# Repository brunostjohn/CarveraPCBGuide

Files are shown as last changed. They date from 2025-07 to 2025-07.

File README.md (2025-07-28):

# How to make double-sided PCBs at home with a Carvera (Air)

This is a super in-progress guide for doing this. There's probably many better ways to do this, this is just what's worked for me.

## Table of Contents

- [How to make double-sided PCBs at home with a Carvera (Air)](#how-to-make-double-sided-pcbs-at-home-with-a-carvera-air)
  - [Table of Contents](#table-of-contents)
- [Materials, Tools, and Software](#materials-tools-and-software)
  - [Software](#software)
  - [Materials](#materials)
  - [Tools](#tools)
- [Preparation](#preparation)
  - [Making a PCB-friendly wasteboard.](#making-a-pcb-friendly-wasteboard)
  - [Making sure copper chips aren't fucking with our mill quality.](#making-sure-copper-chips-arent-fucking-with-our-mill-quality)
- [Going from PCB to Gcode.](#going-from-pcb-to-gcode)
  - [Creating your PCB in KiCAD](#creating-your-pcb-in-kicad)
    - [Quick note about text](#quick-note-about-text)
    - [Board setup](#board-setup)
    - [Pre-export work](#pre-export-work)
    - [Actually exporting the damn thing.](#actually-exporting-the-damn-thing)
  - [Importing your PCB to FlatCAM.](#importing-your-pcb-to-flatcam)
    - [Aligning your sides](#aligning-your-sides)
  - [Adding alignment drills.](#adding-alignment-drills)
  - [Actually making gcode for the align drills.](#actually-making-gcode-for-the-align-drills)
    - [Generating g-code for the front side of the PCB.](#generating-g-code-for-the-front-side-of-the-pcb)
  - [Generating g-code for the back side of the PCB.](#generating-g-code-for-the-back-side-of-the-pcb)
  - [Generating gcode for removing the front solder mask.](#generating-gcode-for-removing-the-front-solder-mask)
  - [Generating the gcode for removing the back solder mask.](#generating-the-gcode-for-removing-the-back-solder-mask)
  - [Generating the gcode for lasering on the front silkscreen.](#generating-the-gcode-for-lasering-on-the-front-silkscreen)
  - [Generating the gcode for lasering on the back silkscreen.](#generating-the-gcode-for-lasering-on-the-back-silkscreen)
  - [Generating the gcode for drills and edge cuts.](#generating-the-gcode-for-drills-and-edge-cuts)
- [Milling the board, lasering the board, and other random side quests.](#milling-the-board-lasering-the-board-and-other-random-side-quests)
  - [Attaching the fixture \& adding the fan.](#attaching-the-fixture--adding-the-fan)
  - [Attaching the PCB.](#attaching-the-pcb)
  - [Finding the 0 point and setting up work coordinates.](#finding-the-0-point-and-setting-up-work-coordinates)
  - [Drilling alignment holes.](#drilling-alignment-holes)
  - [Front copper isolation.](#front-copper-isolation)
  - [Front non-copper clearing](#front-non-copper-clearing)
  - [Back copper isoltion \& NCC.](#back-copper-isoltion--ncc)
  - [Applying the back solder mask.](#applying-the-back-solder-mask)

# Materials, Tools, and Software

## Software

- KiCAD
- Makera's CAM
- Fusion 360
- FlatCAM

  This guide uses the 8.994 beta version of FlatCAM. There _will_ be differences between other versions, but the workflow should stay roughly the same.

## Materials

- Copper-clad FR4, duh.
- UV-curable solder mask (both in target solder mask colour and white, you'll see why).
- Some random ass wood for milling the PCB fixture. (should fit on the Carvera bed)
- TPU to make a spindle fan
- Double sided tape.
- An acetate sheet.

## Tools

- The Carvera Air.
- 3D printer (optional)
- A UV light.
- Shop vac (optional)
- The sanding block that came with the Carvera
- Carvera's Laser Module.
- A 0.2mm corn bit/endmill.
- A 2mm/4mm drill bit.
- Makera's solder mask removal bit.
- Corn bits in other various sizes.
- Drill bits also in other various sizes.
- Something to scrape the PCB off the fixture after the double sided tape. I'm using a 3D printer bed scraper.

# Preparation

## Making a PCB-friendly wasteboard.

The MDF wasteboard on the Carvera isn't super friendly to milling PCBs so we need to make our own thing to which we will attach PCBs. Fortunately enough, I've solved this problem already by making a Carvera friendly thing that can accomodate large-ish PCBs and screws into the bed. It isn't entirely my own creation, it's based on [this guide's](https://hackaday.io/project/202478/instructions) fixture created by [Vedran](https://hackaday.io/vedranMv). I only modified it to hold larger PCBs. You don't need to mill all the holes, it's really only the screwholes that matter. Here's a photo of mine.

Fixture

I made it out of some random wood my landlord had in her shed. Just make if flat enough and you'll be fine.

You can get the [Fusion project here](./projects_and_gcode/fusion/PCB%20fixture%20thing.f3d) or the [STEP file here](./projects_and_gcode/step/PCB%20fixture%20thing.step).

## Making sure copper chips aren't fucking with our mill quality.

When the bit you're using mills it's own chips (or in this case, dust), you get more burrs and more bullshit. To prevent this you can either use a vaccuum attached to your Carvera or a delightful fan.

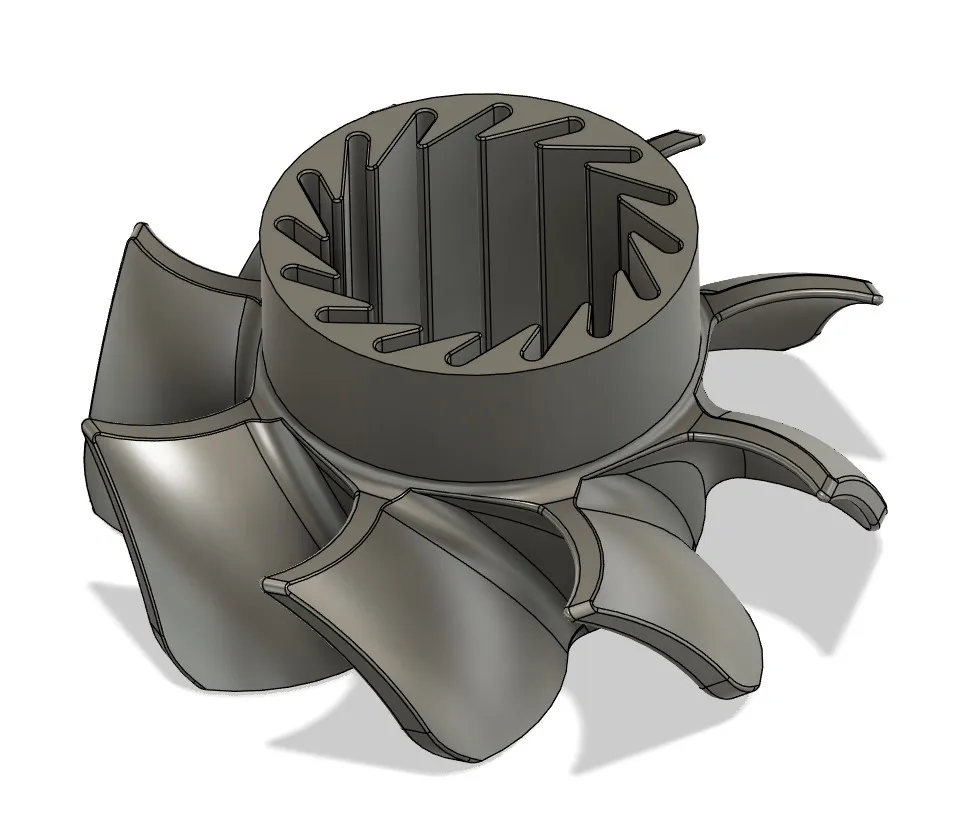
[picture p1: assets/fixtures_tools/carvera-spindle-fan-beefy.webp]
Spindle fan


[RedGT500](https://www.printables.com/@RedGT500_1977691) has already made a great fix to this. A 3D printable fan made out of TPU that's made to go on your spindle. You can even see mine in that photo of the fixture above. You can download it [here](https://www.printables.com/model/1332188-carvera-spindle-fan-beefy-version/files). I've also reuploaded it [here](./projects_and_gcode/step/Spindle%20Fan.step) to protect against link rot.

# Going from PCB to Gcode.

## Creating your PCB in KiCAD

Teaching you to actually make PCBs is outside the scope of this guide. God knows I know fuck all about making PCBs or CNC. What I do know is how I made my PCB so that it works with this process.

This doesn't affect making your schematic, so I'm gonna skip right over to the PCB editor.

### Quick note about text

First, if you think any text you make is gonna look fine, you're sorely mistaken. Don't even bother. Hide all the text and make sure it doesn't end up in the final exports.

### Board setup

Let's move onto the money shot.

- The minimum clearance between tracks should be 0.2mm (you _can_ set 0.1mm and have good results but you have to mind yourself so you don't get the tracks too close together, this is relevant for some smaller ICs or USB-C ports).
- The minimum track width should be 0.2mm (NOT any lower unless you have tiny ass bits, which I don't and haven't tested).
- Your minimum via diameter should be 0.9mm (so that you can drill 0.6mm holes for them). Smaller vias will be a pain in the ass, don't even bother with them.
- Your copper to hole clearance should be 0.25mm. You can go lower (as low as 0.2mm), but I wouldn't recommend it.
- Your copper to edge clearance should be 0mm. This way KiCAD won't force FlatCAM to mill the shit out of the boards edges wasting your time and bit life.
- Your minimum through-hole should be 0.3mm (or the smallest bit you've got).
- Your hole to hole clearance should be 0.2-0.25mm.

### Pre-export work

To make our board show up consistently in the right spot in all of the pieces of software we'll be using, you gotta set a grid & drill/place origin.

In KiCAD's PCB editor, select the `Grid Origin` option.

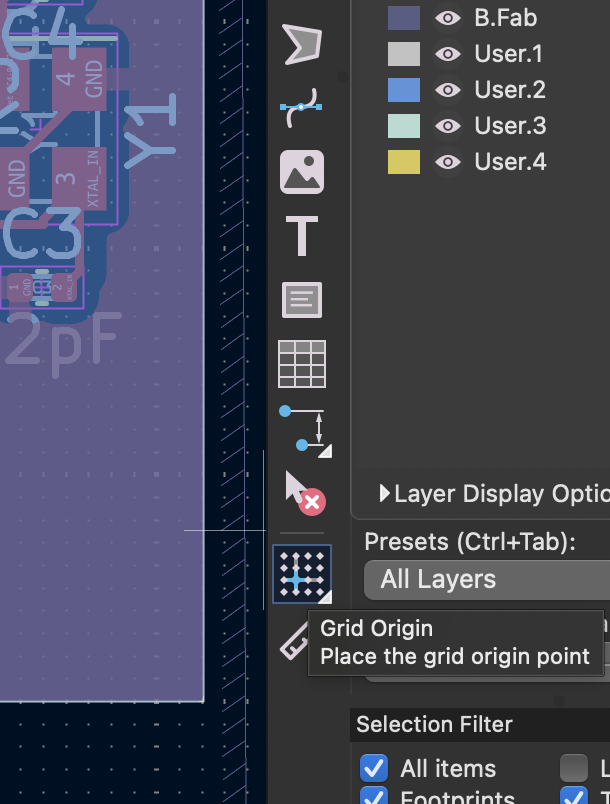
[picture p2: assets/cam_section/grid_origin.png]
Grid origin


Then, place it at the bottom left corner of your board.

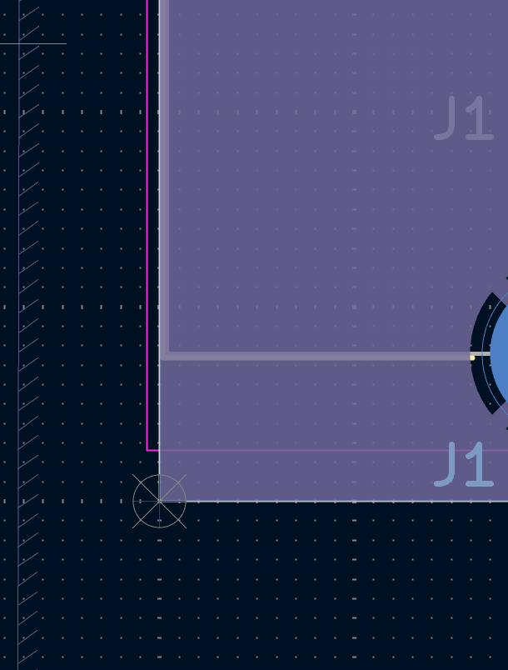
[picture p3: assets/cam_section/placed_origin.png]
Placed origin


Now, press and hold the grid origin button until a second option pops out.

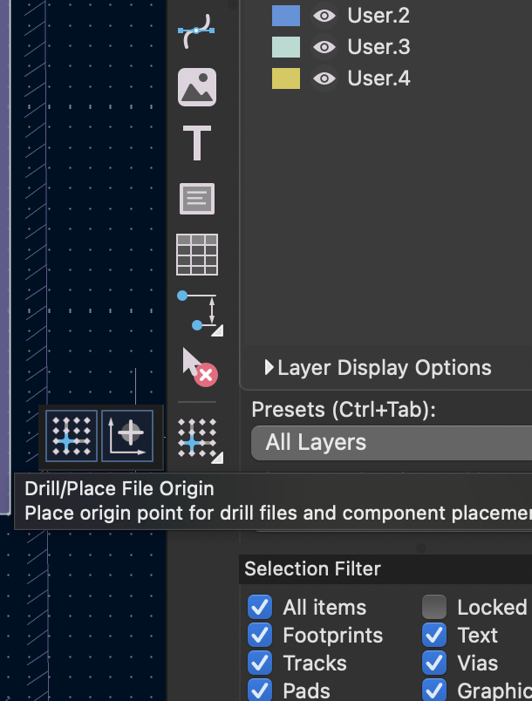
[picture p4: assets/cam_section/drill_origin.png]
Drill origin button


That's the drill origin button. Click on that and place it in the same spot as the grid origin.

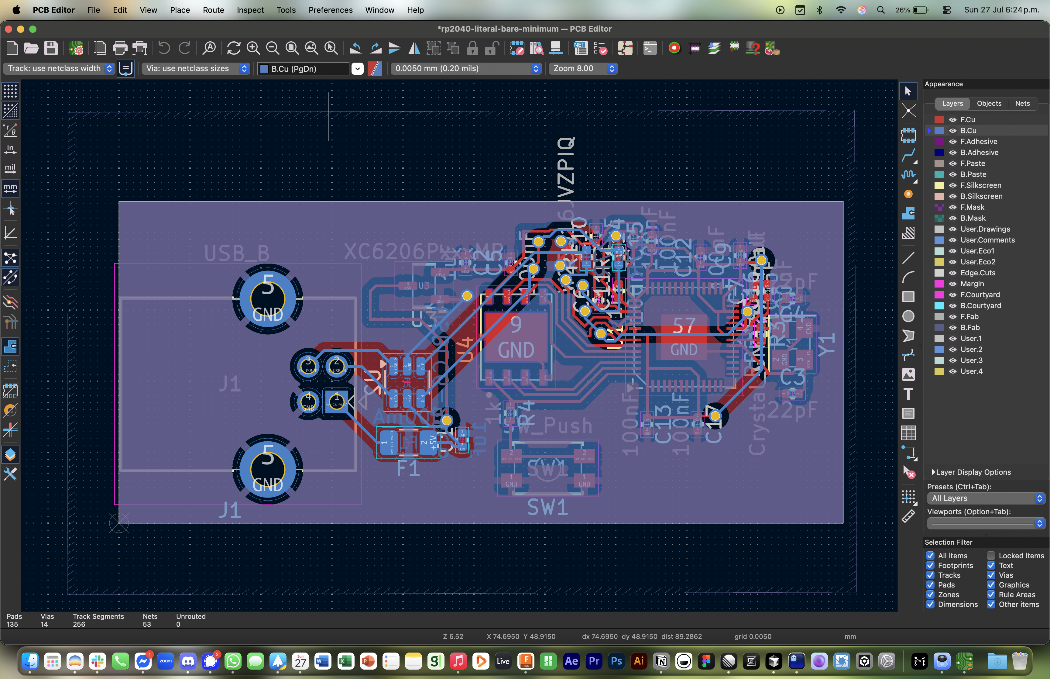
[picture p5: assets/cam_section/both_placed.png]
Both placed


You are now ready to export your board.

### Actually exporting the damn thing.

Click on `File > Fabrication Outputs > Gerbers`.

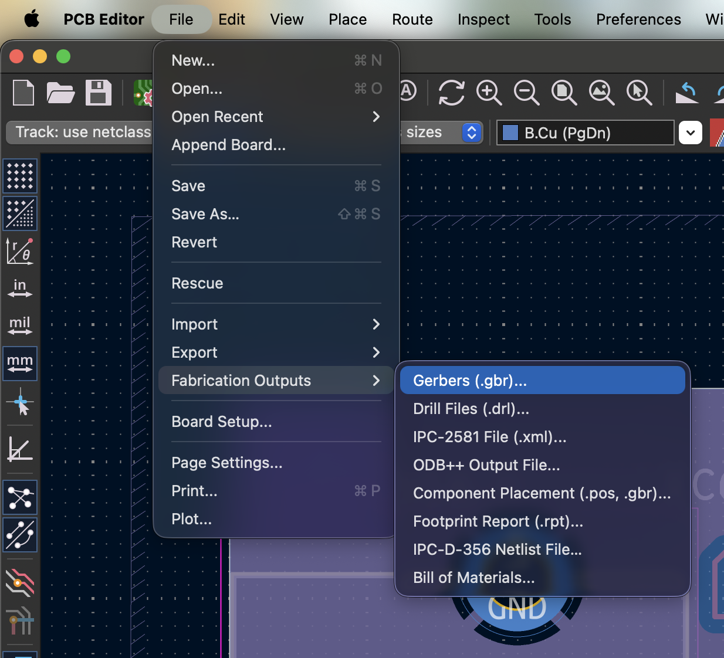
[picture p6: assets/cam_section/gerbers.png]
Export the gerbers on god


Now, select the output folder, select your layers, select `Use drill/place file origin`. First, click on `Generate Drill Files` and also select `Drill Origin > Drill/place file origin`, then click on `Generate Drill File` and close. Then, click on `Plot`. Your board should now have the required outputs to be milled in the folder you selected.

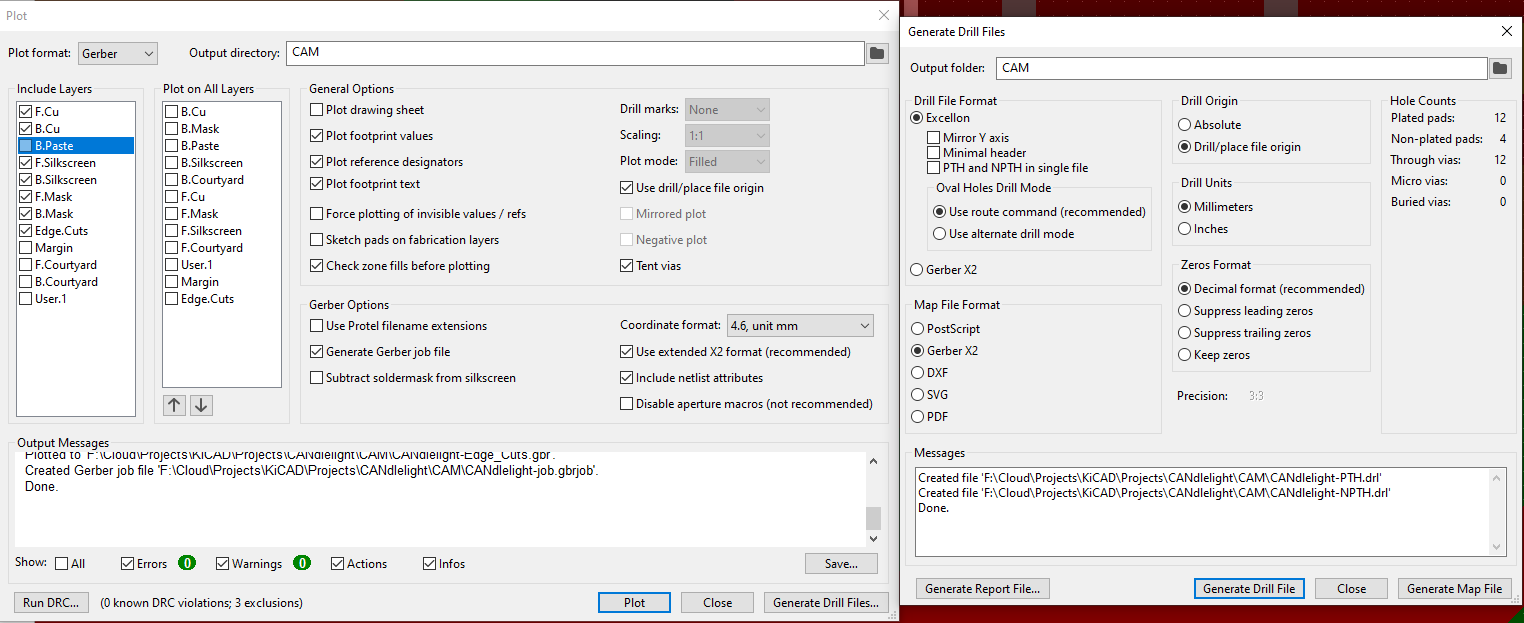
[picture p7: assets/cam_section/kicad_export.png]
Select the right options


(I've taken this photo from [Vedran's guide](https://hackaday.io/project/202478/instructions) because I'm on macOS Tahoe and KiCAD's export window is freaking OUT on it)

You should now have the Gerbers you need to mill your board.

## Importing your PCB to FlatCAM.

Open up FlatCAM and click on `File`. Then hover over `Open` and select `Open Gerber`. **ONLY** import your front and back copper layers. Don't import anything else.

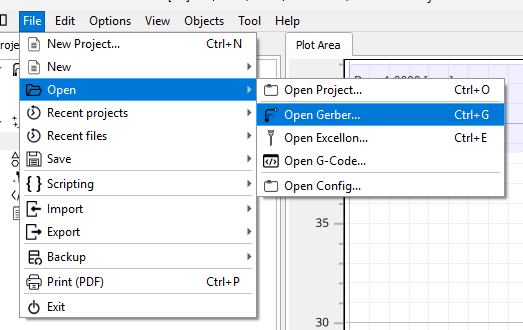
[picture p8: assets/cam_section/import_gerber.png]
Importing the Gerber file


You should see your board on the newly opened side panel:

Newly imported board

To make seeing them a little bit easier, feel free to select whatever colours you think they should have:

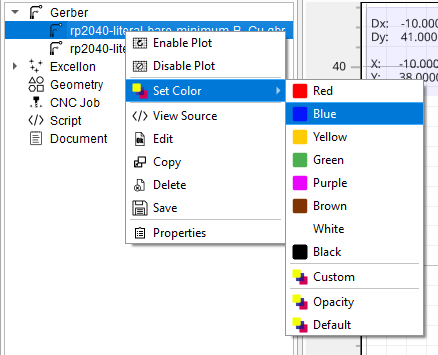
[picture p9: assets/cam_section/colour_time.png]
Selecting colours


Having done that, you should see something like this:

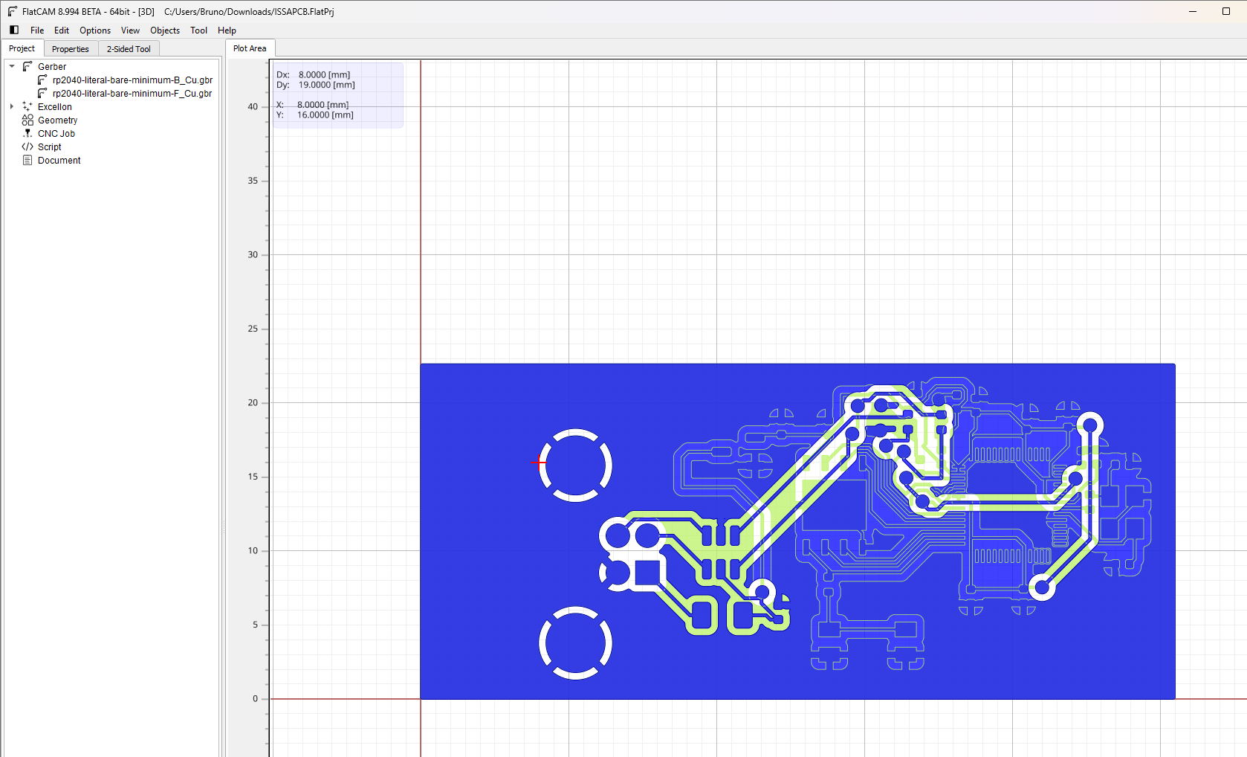
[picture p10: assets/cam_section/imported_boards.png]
Imported boards


### Aligning your sides

It may seem like the boards are in the right orientation, but that is not the case. Remember, this is a 2D program and if you flip over the board, you will notice that it's almost as if it's _mirrored_. Let's fix that.

At the top of the UI, click on `Tool` and select `2-Sided PCB`:

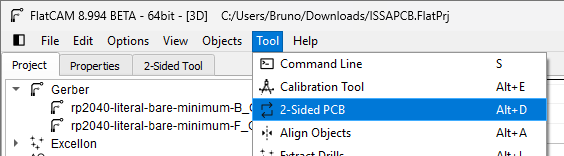
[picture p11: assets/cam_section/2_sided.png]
2 sided option


This will take you to a panel that looks something like this:

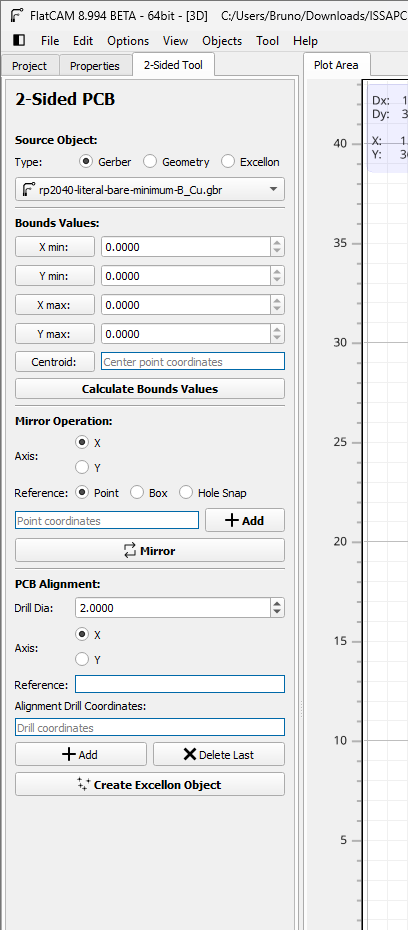
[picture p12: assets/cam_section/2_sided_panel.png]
2 sided panel


First, as the source object, select the _back side of the board_. I know that that's confusing, but this is the object that will end up getting mirrored. Horrible naming, but we can work with that.

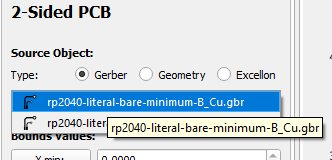
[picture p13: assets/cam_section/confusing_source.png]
Source object panel


Let's now mirror our back side. in the Mirror Operation section of the 2-Sided PCB panel, select the X axis for your mirror operation (we'll be flipping the board over on its long side) and select Box as your reference. I've seen a YouTuber use Point and do some crazy ass math, but that's quite silly considering we're on a computer that can _compute_ it for us.

Next, as your reference object, select the front side of your board. If you've done this right, your Mirror Operation panel should look something like this:

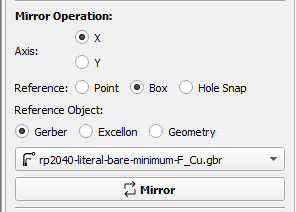
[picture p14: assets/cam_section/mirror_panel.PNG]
Mirror panel


Looks great! Let's press Mirror to get it onto the right side. Things will feel a bit wrong now. If you've done this right, this is what it should look like:

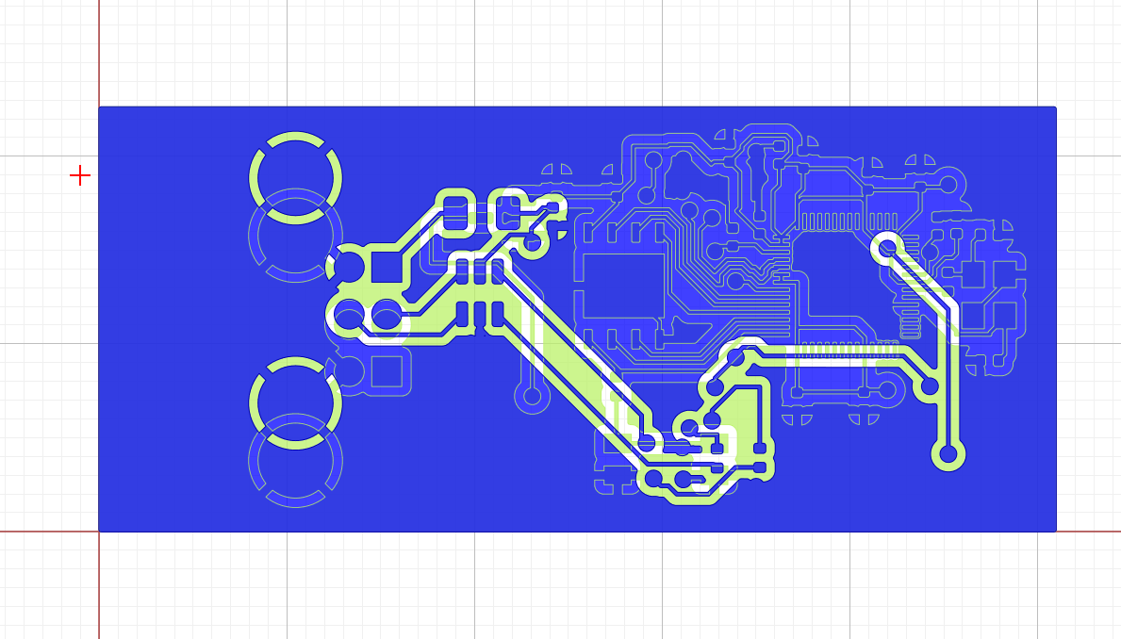
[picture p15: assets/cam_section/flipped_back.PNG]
Flipped back


This seems wrong because our vias are not aligned. Remember, this is _Flat_ CAM. So what is happening here instead is that we're looking at our boards from the _top_, just like our CNC will. This means that if you physically flip over your soon-to-be board, you will see the same view as you are right now in FlatCAM.

## Adding alignment drills.

We're almost done with the 2-Sided PCB tool. All we need to do now, is make sure that we can somehow reliably align both sides on our CNC's work area. If you've ever done this manually, you'll know that it's basically impossible.

In the PCB Alignment section, set your drill diameter to the size of your alignment pins. I'm using the 2mm diameter dowel pins that came with the PCB fabrication toolkit, but you can use 4mm if you haven't bought it and are using the slightly larger pins that come with the machine itself.

PCB align drills

To do this accurately, we need to do some math.

Let's figure out where our alignment pins should be. Go back to the project tab in FlatCAM and find the front side of your board. Right click on it and select `Properties`.

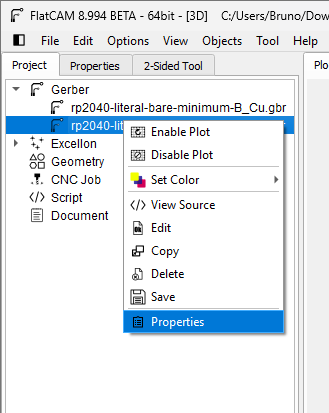
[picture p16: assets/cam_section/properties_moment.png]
Properties option


In there, you will see a dimensions section. This contains what we're looking for, the **Length** and **Width** of the board:

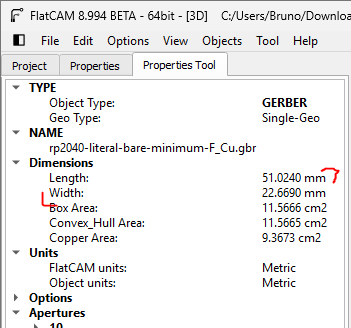
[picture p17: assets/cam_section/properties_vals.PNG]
Properties values


Make note of these and go back to the 2-Sided PCB tool like shown before.

In the PCB Alignment section, there will be a text field titled `Alignment Drill Coordinates`. We're calculating these because it's gonna be hard to get this right manually.

We want 4 drills on opposite corners of the board 3mm away from the board itself.

So what we want is:

- **A hole on the bottom left.**
  In my case, it's at `(0.0, -3.0)` because we're to the leftmost corner of the board, 3mm away from the bottom edge.
- **A hole on the top left.**
  In my case, that's `(0.0, 25.669)` because I want it on the same "line" as the left edge but 4mm away from the top edge (so $22.669+3=25.669$).
- **A hole on the bottom right.**
  In my case, that's at `(51.024, -3)` because we're at the rightmost corner of the board, 3mm away from the bottom edge.
- **A hole on the top right.**
  For me, that's at `(51.024, 25.669)` because I want it on the same "line" as the right edge but 4mm away from the top edge (so $22.669+3=25.669$).

This, in aggregate, is:
```(0.0000, -3.0000),(51.0240,-3),(0, 25.6690),(51.0240,25.6690)```

Let's punch these numbers into FlatCAM and click on `Create Excellon Object`.

![Excellon creation](./assets/cam_section/excellon_time.PNG)

You should now see your alignment drills on the Plot Area.

![Drills in plot area](./assets/cam_section/align_in_plot.PNG)

## Actually making gcode for the align drills.

I don't trust FlatCAM with doing these drilling ops. Partly because I'm not super familiar with it and partly because MakeraCAM makes it dead easy. Let's open up a new 3-axis project in MakeraCAM.

![Opening MakeraCAM for the drills](./assets/cam_section/makera_moment.PNG)

Now, set up your stock. Pick the PCB material and set the XYZ values to anything that fits with your board.

![Stock selection](./assets/cam_section/makera_drills_stock.PNG)

Now we're ready to drill some shit. Let's export our fresh Excellon drills from FlatCAM.

![Export drills](./assets/cam_section/export_drills.PNG)

Save them somewhere they won't get lost and get back to MakeraCAM. In the layer panel, right click 2D layers and select `Import Graphic > Import PCB`.

![Import PCB](./assets/cam_section/import_drills.PNG)

Once you import your drills, you should be able to see them in the layers panel and in the work area. Don't worry if the size is slightly wrong, that's okay.

![Drills in work area](./assets/cam_section/drills_in_work.PNG)

You'll also notice that they go outside of the "work area". **Don't move them by even a millimetre**. Just leave them as-is. This is fine and will be rectified later when we go to drill them.

Select all your drills by using MakeraCAM's `Select Graphics` options:

![Selecting drills](./assets/cam_section/select_drills.PNG)

You should see them all get kind of dashy. With them selected, go into 2D toolpaths and select 2D drilling.

![Selecting the toolpath](./assets/cam_section/drilling_toolpath.PNG)

Let's sort out the settings. I'm using my 2mm drill. I used a clearance height of 5mm because there's nothing in the way of the toolhead as these drills are being created. Use feeds & speeds for PCBs. Your wooden base and bit will be fine (I think?). We're drilling 6mm down because the dowel pins are about 10mm in height, and we want them to be secure.

![Selecting the settings](./assets/cam_section/drilling_settings.PNG)

That's it! You're now ready to drill your alignment drills. Let's move onto generating the gcode for our top and bottom layers.

### Generating g-code for the front side of the PCB.

Let's go back to FlatCAM. Double click on the front layer of your PCB. That should bring you to this panel:

![Gerber panel](./assets/cam_section/gerber_panel.PNG)

We will start by electrically isolating your traces. This removes material around only the traces. Click on `Isolation Routing`. You will now see a different panel:

![Isolation panel](./assets/cam_section/iso_tool.PNG)

We will lie about our bits diameter. This is so that FlatCAM actually mills them. Your tool's supposed to be smaller than your traces. But it's fine if it's equal to their width. So fuck it, let's lie. It _does_ work. Double click what's currently in there and type in 0.19. This will make some of your traces slightly undersized. For me, that's worked out okay but YMMV. Then select the tool type. We're using a corn bit so any of the CX options are fine. Let's pick C1 for the vibes.

![Tool type](./assets/cam_section/tooltype.PNG)

Now, right at the bottom, click on `Generate Geometry`. This will create geometry for us that we can later use to CNC the board.

You will see a bunch of toolpath parameters. In the path type, select `Iso`:

![Iso path](./assets/cam_section/iso_path.PNG)

I'm setting my cut Z to -0.05. That's enough to get the copper off the board and get to the FR4 for me. Things might be different for you, so experimentation is king here. I'm using an XY feedrate of 120 and Z feedrate of 60. These tools are mad fragile so it's better to not fuck about. I'm also using a spindle speed of 15k because I've gotten the best results that way.

![Iso speeds feeds](./assets/cam_section/speeds_feeds.PNG)

When you're done, click on `Generate CNCJob object`. This will generate actual gcode we can use. You will now see an actual toolpath forming. The panel will also give you an option to save your gcode. Do that and open the generated file in Notepad.

For the gcode-inclined among us, you'll notice that T1 and M6 are on separate lines:

![Bad gcode](./assets/cam_section/wronglines_gcode.PNG)

This makes the Carvera very angry. It stops the job and loses its heightmap. It's a nice machine so let's not make it angry. Delete the newline between these, add a space, and save. Here's what a fixed file looks like:

![Unfucked newline](./assets/cam_section/unfucked_newline.PNG)

You'll need to do this for every CNCJob you save from FlatCAM. There's probably a fix for this. I haven't found it yet.

Let's now get back to the Project tab in FlatCAM. Double click on your front layer again. This will open up the Gerber Object panel again. This time, click on NCC Tool. That is the **n**on-**c**opper **c**leaning tool. Once again select the C1 tool type and a diameter of 0.19. Generate your geometry. Now, sometimes, that takes ages. Let it cook. It might complain that it couldn't fully isolate.

![FlatCAM hating](./assets/cam_section/flatcam_hating.PNG)

Sometimes it might even tell you where the polygons it failed to clear are. Double check that everything is still fine. It probably is.

Once you do, configure your toolpath. Most, if not all, of the settings will be the same as for isolating traces.

![NCC config](./assets/cam_section/ncc_config.PNG)

Once you're satisfied, click on the `Generate CNCJob object button`. Verify your toolpath and save your CNC code. Repeat the same steps as for the isolation gcode where we had to remove a newline from there.

## Generating g-code for the back side of the PCB.

Repeat the steps you did for the front side, just for the back side this time.

We're now officialy done with FlatCAM. We don't need to look at it again (yay!).

## Generating gcode for removing the front solder mask.

Let's open up a new 3-axis project in MakeraCAM.

![Opening MakeraCAM for the drills](./assets/cam_section/makera_moment.PNG)

Now, set up your stock. Pick the PCB material and set the XYZ values to anything that fits with your board.

![Stock selection](./assets/cam_section/makera_drills_stock.PNG)

In the layer panel, right click 2D layers and select `Import Graphic > Import PCB`.

![Import PCB](./assets/cam_section/import_drills.PNG)

Select your _front copper layer_. I know you'll be tempted to use the solder mask gerber. Because the solder mask gerber won't remove mask from the vias, It's not particularly useful to us.

Once you import your layer, it should look something like this:

![Imported layer](./assets/cam_section/imported_pcb_soldermask.PNG)

You'll notice MakeraCAM helpfully created a pad layer for us. That's what we'll be primarily working with. Let's hide the non-pad layer.

![Hidden non-pad layer](./assets/cam_section/hidden_nonpad.PNG)

Right click on your pad layer and click on `Select graphics` to select all our pads & vias.

With that selected, select the 2D Pocket toolpath from the 2D options.

![2D pocket time](./assets/cam_section/2d_pocket_soldermask.PNG)

For this pocket, we are using the solder mask removal tool.

![2D pocket options](./assets/cam_section/soldermask_pocket_options.PNG)

We're using a taller clearance height to avoid fucking the tool into our dowel pins. An end depth of 0.3mm has delivered solid results to me, but in the worst case one can re-run the toolpath with a higher depth. Anyways, let's run calculate.

Great! It seems like everything was calculated. Wait, not everything. Some of the pads are too small!

![Smol pads](./assets/cam_section/them_pads_too_big.PNG)

Don't worry, I have a trash quality solution to this that works unnecessarily well.

Start by holding down `Shift` and left clicking on pads that weren't generated. Group this by the _size of the pad_. So for example, I'm not gonna do the RP2040 pads because they're small as fuck. We'll start with the NOR flash:

![NOR flash selected](./assets/cam_section/norflash_selected.PNG)
Now, let's create a new pocket toolpath. Same settings as before with one change. We will use the offset option.

![NOR with offset](./assets/cam_section/offset_moment_nor.PNG)
This will force MakeraCAM to generate a toolpath by making it pretend our selected graphic is larger than it actually is. This _does_ make pads slightly larger than they should be. But in reality, with our NCC toolpaths and solder mask spread, this usually means that the extra removed soldermask is still kind of there because it goes deeper than the tool does. You'll see that in a photo later.

Now, let's do the RP2040 pads (as an example of some smaller pads). let's start with the ones oriented horizontally. Do the same offset trick. Here's where it gets funky. These pads are small as shit so ripping them off is SUPER easy. You want to _minimise the amount of time the tool spends on the pad_. And also, you want to minimise the pad itself. So experiment until you find the smallest possible offset that makes the machine mill the pads.

![Horizontal pads](./assets/cam_section/horizontal%20pads.PNG)
This will take experimentation. Take your time with it. Do the same for the vertical pads now.

When you're done, your Carvera should have toolpaths for all your pads.

![Done](./assets/cam_section/soldermask_front_done.PNG)

Export your gcode and save for later.

## Generating the gcode for removing the back solder mask.

Take your mirrored back board from FlatCAM and export the Gerber. Import to MakeraCAM and mirror it vertically:

![Mirror vertically](./assets/cam_section/mirror_vertically.PNG)

## Generating the gcode for lasering on the front silkscreen.

Let's open up a new 3-axis project in MakeraCAM.

![Opening MakeraCAM](./assets/cam_section/makera_moment.PNG)

Now, set up your stock. Pick the PCB material and set the XYZ values to anything that fits with your board.

![Stock selection](./assets/cam_section/makera_drills_stock.PNG)

In the layer panel, right click 2D layers and select `Import Graphic > Import PCB`.

![Import PCB](./assets/cam_section/import_drills.PNG)

Import your front silkscreen layer.

![Imported silkscreen](./assets/cam_section/imported_silkscreen.PNG)

Any text you have needs to go. I haven't figured out how to make it legible yet but it'll legitimately look like trash.

![Proof board with text](./assets/cam_section/proof_board_again.jpg)

Just delete it.

![Removed text](./assets/cam_section/bye_text.PNG)

Now, this part you can only do after experimenting a little bit. The laser is _very_ slightly off from where the mill ends up. This will cause your silkscreen to be off. I still haven't gotten the right offsets, but here's how to apply them.

Right click your silkscreen layer in the layers section of MakeraCAM and click on `Select Graphics`.

![Selecting graphics](./assets/cam_section/select_drills.PNG)

Now, click on the transform menu and select `Move`.

![Selecting move](./assets/cam_section/transform_move.PNG)

You will be brought to a delightful panel for moving shit. It'll tell you your current selection's location:

![Move panel](./assets/cam_section/move_panel.PNG)

Now, my last proof board turned out like this:

![Fucked up proof board](./assets/cam_section/proof_board.jpg)

It looks like on the X axis we are too far to the right (so, we need to compensate by subtracting) and on the Y axis we are too far to the bottom (so we need to compensate by adding).

I'm gonna try -0.75mm on the X axis and +0.3mm on the Y axis.

Based on the values in the move panel:

- X axis
  $24.579-0.75=23.829$
- Y axis
  $11.161+0.3=11.461$

Let's type that into MakeraCAM.

![Moved laser](./assets/cam_section/moved_laser.PNG)

Great, with our paths translated we're ready to create our laser toolpaths.

Now, this is very important, **select things by their thickness**. Group things as thick as each other together. This way, you can get a result that doesn't look like shit.

In my case, there's only a few tiny bits that have the same thickness. Let's select everything else for now.

![Selected things](./assets/cam_section/unselected.PNG)

From the laser toolpaths dropdown, select Laser Vector.

![Laser vector](./assets/cam_section/laser_vector.PNG)

As for settings, set speed at a hilariously low 30mm/min and power at 3%. We're not actually trying to engrave or cut anything (you'll see when we actually run the toolpaths), we're exploiting the laser's wavelength to use it to selectively cure the white soldermask. Set the indent distance at _the lowest possible value that still generates a complete toolpath_. Pair that with using the laser in line mode. The thinnest laser path can generate the thickest solder mask, so it's better to err on the cautious side.

![Laser settings](./assets/cam_section/laser_settings.PNG)

Now, thing by thing generate your thicker paths with the appropriate indent distances. The thicker it is, the higher the indent distance should be.

With all the toolpaths done, you can now export your gcode and stash it for later.

![Laser done](./assets/cam_section/done_laser.PNG)

## Generating the gcode for lasering on the back silkscreen.

About the same as the front silkscreen. Just with the caveat that you have to mirror it vertically as shown in the previous sections.

## Generating the gcode for drills and edge cuts.

This will be the last toolpath for our PCB.

Let's open up a new 3-axis project in MakeraCAM.

![Opening MakeraCAM](./assets/cam_section/makera_moment.PNG)

Now, set up your stock. Pick the PCB material and set the XYZ values to anything that fits with your board.

![Stock selection](./assets/cam_section/makera_drills_stock.PNG)

In the layer panel, right click 2D layers and select `Import Graphic > Import PCB`.

![Import PCB](./assets/cam_section/import_drills.PNG)

Import your PTH, NPTH, and edge cut layers.

![Imported drills](./assets/cam_section/imported_pth_npth_edge.PNG)

For creating drill holes, there are 2 strategies. You can use a 2D Pocket toolpath or a 2D Drill toolpath. The drill toolpath is greatly preferred because it risks your pads less. If you don't have the right sized drills though, you can make do with a pocket and very often your PCB will be okay. We will use both strategies here because it's fun.

Let's start by using plain ol' drills. Right click the layer that has the right sized drills for your bits and click on `Select Graphics`.

![Select graphics](./assets/cam_section/select_drills.PNG)

Now, select the 2D Drilling toolpath from the 2D toolpaths dropdown.

![Select toolpath](./assets/cam_section/pth_drillin.PNG)

As for the settings, you want to drill 1.6mm down to ensure you go fully through the board. This will make a delightful hole in your wooden block. That's fine because the bit should survive this blunder. Remember to use a drill that matches your layer drill size.

![Drilling settings](./assets/cam_section/pth_settings.PNG)

Now, let's do the pleb way of drilling a hole - the 2D pocket toolpath. Select the drills you don't have the proper bits for and select 2D Pocket from the 2D toolpaths dropdown.

![The pleb way to do drills](./assets/cam_section/pth_pleb_way.PNG)

Select a corn bit smaller than your smallest drill size. Make it mill 1.6mm down to make sure we get all of the board.

![Corn bit](./assets/cam_section/pth_corn_bit.PNG)

For the strategy, we're doing outside in. I've gotten the best results with that.

![Outside in](./assets/cam_section/pth_outside_in.PNG)

Almost done with our last toolpath! Let's cut the board out of the stock. Now, edge cuts are sneaky little shits. It doesn't look like it, but there's two of them. Zoom in and delete the smaller one.

![Delete him](./assets/cam_section/dual_contour.PNG)

Select your edge cut (NOT cuts!) and select the 2D Contour toolpath from the 2D toolpaths dropdown.

![Edge contour](./assets/cam_section/edge_contour.PNG)

For these, use your _biggest_ corn bit. Otherwise, it'll look like shit. Again, cutting 1.6mm down.

![Big corn bit](./assets/cam_section/bigass_corn.PNG)

To not end up fucking our board, pick the outside strategy.

![Outside](./assets/cam_section/outside_cuts.PNG)

Last one, so the board doesnt go flying out of the FR4, add some tabs. Click on custom, make them triangle shaped, and select `Add`.

![Adding tabs](./assets/cam_section/add_em.PNG)

Now, click roughly in the centre of each edge of the contour.

![Adding tabs, still](./assets/cam_section/gimme_tabs.PNG)

Sick. Now press `Exit Add` and calculate your toolpath.

![Contour path](./assets/cam_section/contour_path.PNG)

You can now export your g-code. Since we're using many corn bits, MakeraCAM will complain about tool numbers. Change them up until you're happy with the numbers. Just make each tool have a different one.

With your g-code exported, you're now ready to mill some shit. Let's get to making everything.

# Milling the board, lasering the board, and other random side quests.

## Attaching the fixture & adding the fan.

Let's get started by screwing in the fixture and adding the fan. Take anything in the spindle out of the spindle and press fit the fan. After that, reference the photo below to see where the fixture screws in. Use the medium-long screws that come with the Carvera.

![Fixture and fan](./assets/fixtures_tools/fixture.jpg)

## Attaching the PCB.

Put double sided tape all over the back of the PCB.

![Tape on the PCB](./assets/milling_section/start_double_sided_tape.jpg)

Then, stick it on the fixture. Avoid putting any drills around the screws at the bottom of the fixture. Make sure there's enough space to flip the board over while keeping the entirety of it on the fixture itself.

![Attached PCB](./assets/milling_section/attached_pcb.jpg)

Feel free to use the roller from the PCB fabrication kit (if you bought it) to ensure the adhesive is nice and squished.

![Squishing operations](./assets/milling_section/attach_to_fixture_with_roller.jpg)

## Finding the 0 point and setting up work coordinates.

Insert the leveling probe into the spindle.

![Probe](./assets/milling_section/insert_probe.jpg)

Let's open up the Carvera Controller. Connect to the machine and click on the top right button. Then, select the device diagnose menu. In there, turn on the probe laser.

![Probe laser](./assets/milling_section/probe_laser_turned_on.jpg)

You will see the laser come alive. Now, exit the diagnose menu and go into the manual control menu.

![Manual control menu](./assets/milling_section/manually_move.png)

Here, move the toolhead until the laser pointer is pointing at where you want the X and Y zero points to be (where the PCB starts). Remember that some of the align holes are at minus points when doing this. If you feel like things are moving too slow or too fast, change how fast the Carvera moves the axes.

![Speed change](./assets/milling_section/move_by.png)

Find your zero point.

![Zero point](./assets/milling_section/pcb_xy_0_point.jpg)

Once you're happy with the zero point, let's start running the alignment hole job.

## Drilling alignment holes.

![Align job](./assets/milling_section/upload_drills.png)

When you click on start job, you will see a work origin and leveling menu. Your toolhead is at the X and Y zero point right now. Let's let the machine know about that by clicking `Config` under `Set Work Origin` and setting the anchor as `Current Pos`.

![Current Pos anchor](./assets/milling_section/current_pos.png)

Let's move onto leveling. You don't need to go super crazy here, the drills just need to be accurate enough.

![Leveling config](./assets/milling_section/align_drills_leveling_config.png)

Let's start our job and wait until it's done.

![Waiting](./assets/milling_section/running_drills.png)

Okay, there's holes now! Get rid of the debris using a vacuum.

![Holes](./assets/milling_section/pin_holes_drilled.jpg)

After you've cleared them, put the dowel pins in. From now on, **anytime you're machining the board the dowel pins should be in it**. That will prevent unnecessary movement and ensure alignment.

![Pins in](./assets/milling_section/pins_in_holes.jpg)

## Front copper isolation.

Let's move onto the fun stuff. Load up the copper isolation job.

![Iso job](./assets/milling_section/run_f_iso.png)

**DO NOT** change the work origin settings. These will now stay the same for the entire duration of us milling this board.

We will change the levelling settings though. We want to be absolutely certain we have all the weird imperfections accounted for. Use 15 levelling points. Yeah, it's a lot. Yeah, it'll take ages. And yeah, it's worth it.

![Hella points](./assets/milling_section/from_now_on_probe_a_lot.png)

Great! Let's wait for our machine to be done.

![Waiting for iso](./assets/milling_section/wait_for_iso.png)

Nice result!

![Done iso](./assets/milling_section/post_iso.jpg)

## Front non-copper clearing

Let's now move onto milling out the non-copper sections. Load up the NCC job.

![Load NCC](./assets/milling_section/run_ncc.png)

Now, before you run it, **DO NOT** enable any option that requires the probe. We want the Carvera to reuse it's heightmap. Doing that will cause it to clear it and you'll get worse results.

![NCC options](./assets/milling_section/disable_everything_with_probe.png)

Let's wait for NCC to be done.

![Waiting for NCC](./assets/milling_section/ncc_wait.png)

## Back copper isoltion & NCC.

With front NCC done, we can scrape the board off our fixture. Add double sided tape _only above and below the board_. If you add tape onto the board, you run the risk of scraping traces.

Just like with the front side, run maximum leveling (15 points) and start the isolation job. Once done, start NCC without using the probe. Once that's done, we're ready to move onto solder mask.

## Applying the back solder mask.

Right now, the board will have a bunch of burrs. We don't want that as it will cause an uneven stick & coat for the UV-curing solder mask. Fortunately, Makera includes a fine enough sanding block with the Carvera.

![Sanding block](./assets/milling_section/sanding_block.jpg)

Rub that shit on the board until it gets nice and shiny.

![Rubbing it on god](./assets/milling_section/shinier_board.jpg)

Now, the sander itself leaves some nasty shit on the board. Grab some isopropanol and swab it off.

![Swabbing](./assets/milling_section/isopropanol_thing.jpg)
![Cleaning](./assets/milling_section/cleaning_up.jpg)

As you can see, that is quite nasty.

![Ew](./assets/milling_section/this_shit_dirty.jpg)

Okay, grab your favourite solder mask.

![Solder mask time](./assets/milling_section/solder_mask_time.jpg)

Apply it evenly-ish on the board.

![Solder mask applied](./assets/milling_section/applied_mask.jpg)

Now, grab a transparent sheet. I'm using some random acetate sheets I had at home.

![Sheet](./assets/milling_section/transparent_sheet.jpg)

Squish it on the board.

![Squished](./assets/milling_section/squished.jpg)

Now, use the roller that comes in the PCB fabrication kit (or a credit card) to get the solder mask spread evenly (enough) on the board.

![Rolling](./assets/milling_section/they_see_me_rolling_they_hating.jpg)

Once you're done, you should be left with something that looks kind of like this.

![Rolled and squished](./assets/milling_section/post_roller.jpg)

Now, grab your favourite UV light, set it to at least 15 minutes, and start curing this thing.

![Curing](./assets/milling_section/curing_that_shit.jpg)

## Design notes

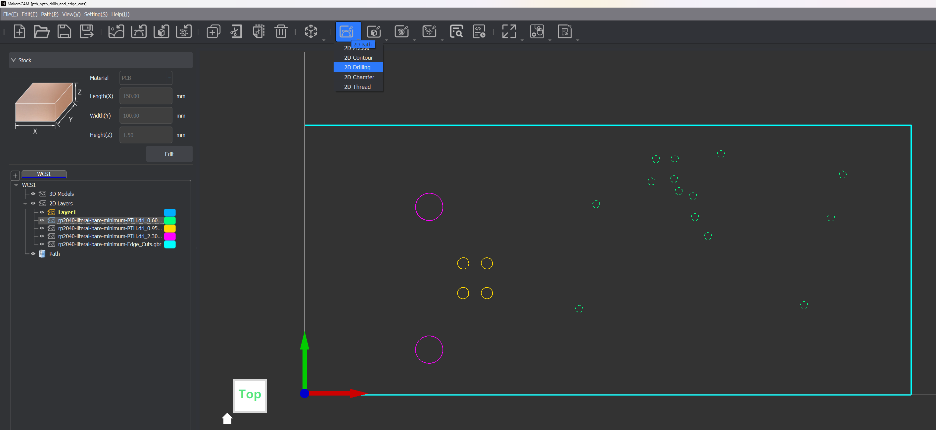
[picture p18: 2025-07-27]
assets/cam_section/pth_drillin.PNG

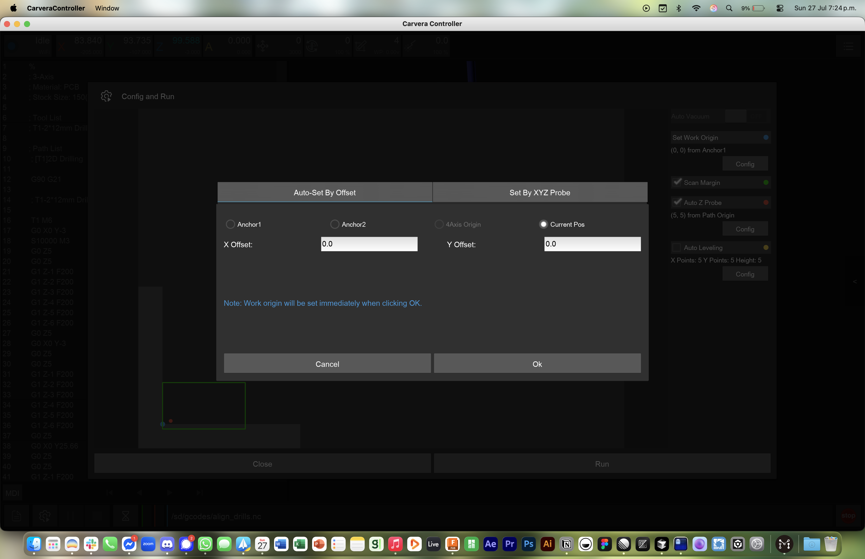
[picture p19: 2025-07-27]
assets/milling_section/current_pos.png

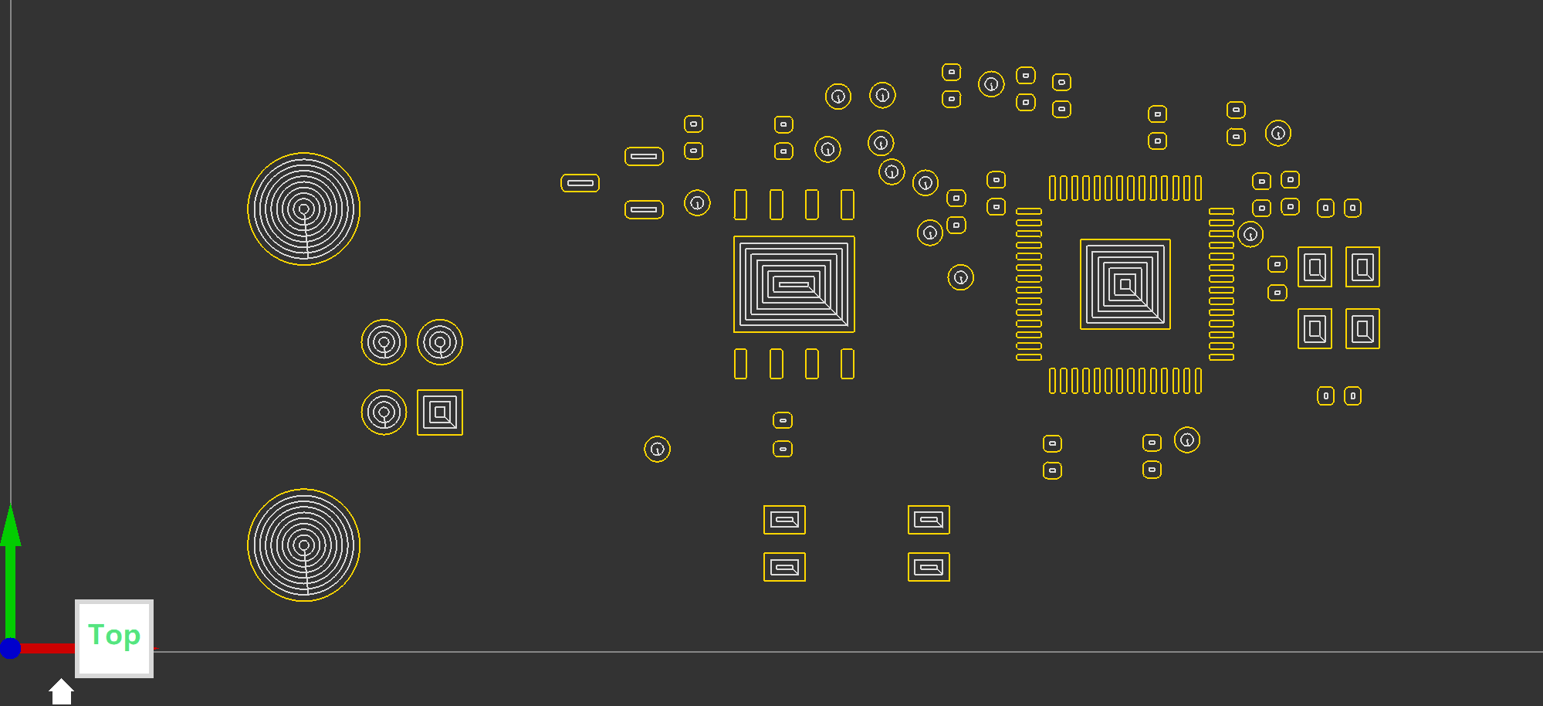
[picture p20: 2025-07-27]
assets/cam_section/them_pads_too_big.PNG

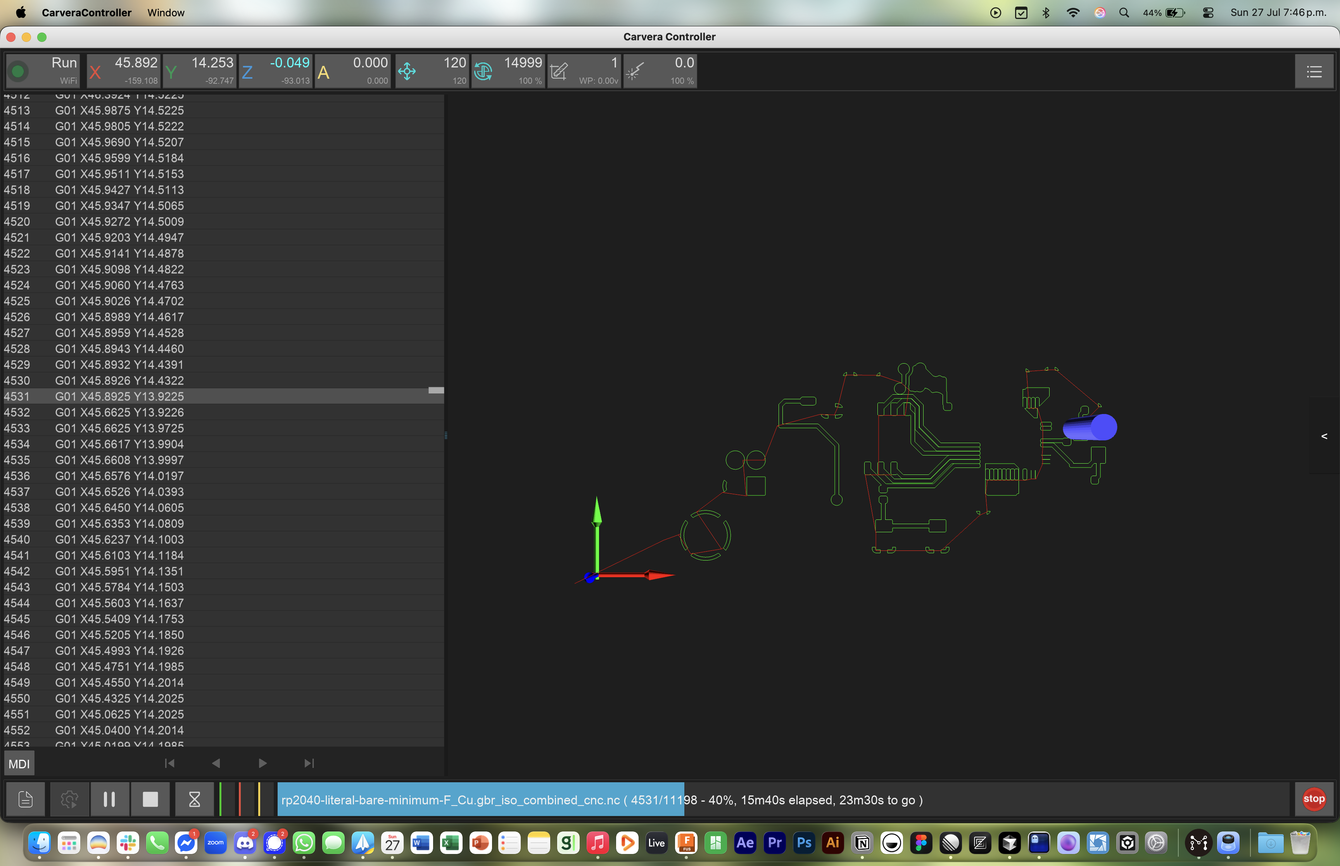
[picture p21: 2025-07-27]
assets/milling_section/wait_for_iso.png

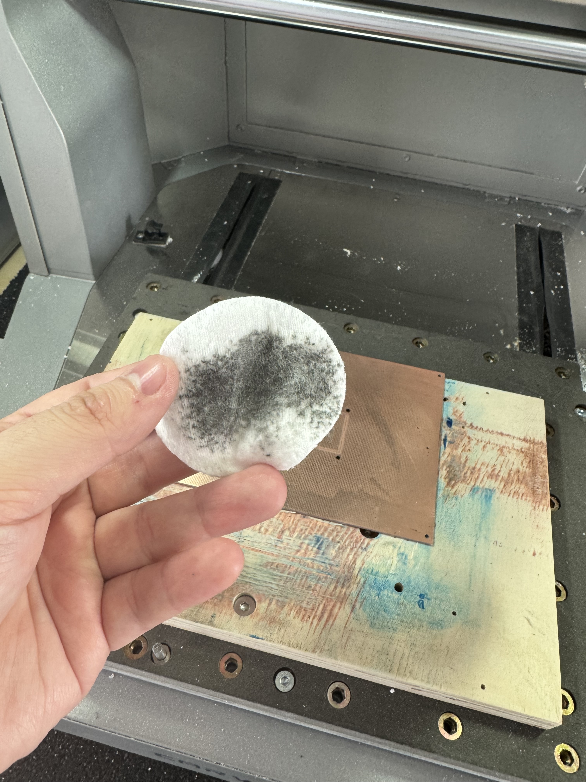
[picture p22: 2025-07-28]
assets/milling_section/this_shit_dirty.jpg

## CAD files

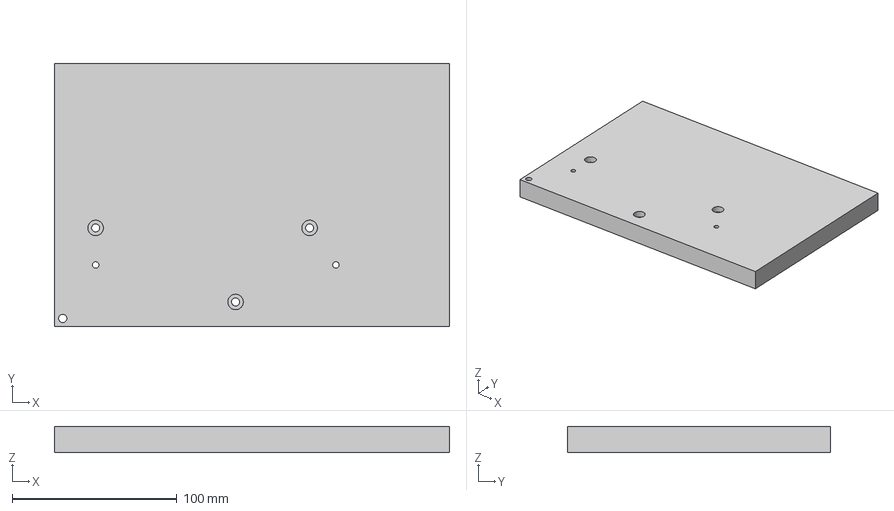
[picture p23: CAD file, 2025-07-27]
projects_and_gcode/step/PCB fixture thing.step
240.0 x 160.0 x 16.0 mm

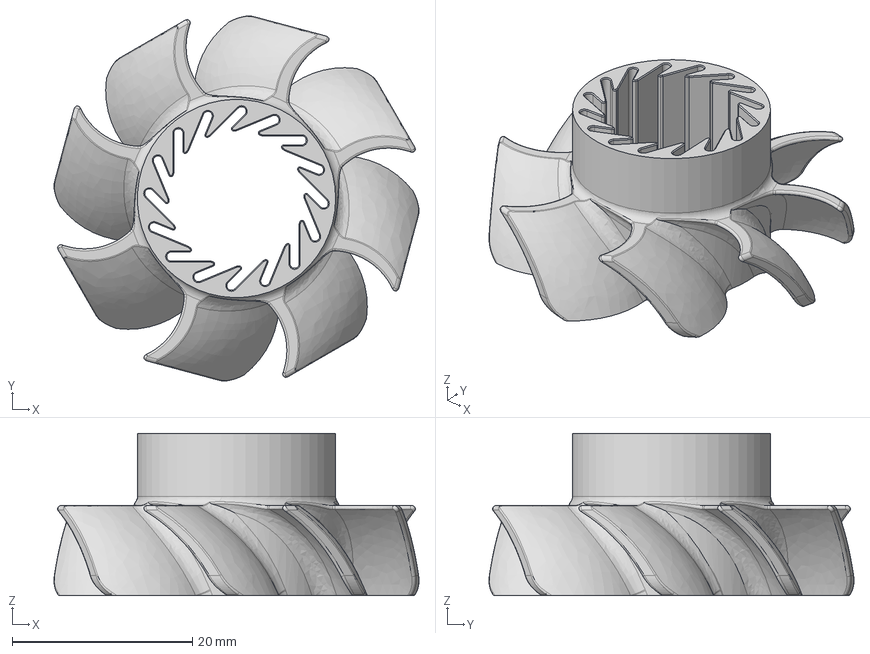
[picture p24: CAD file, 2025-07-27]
projects_and_gcode/step/Spindle Fan.step
40.5 x 40.5 x 18.0 mm

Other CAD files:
projects_and_gcode/fusion/PCB fixture thing.f3d

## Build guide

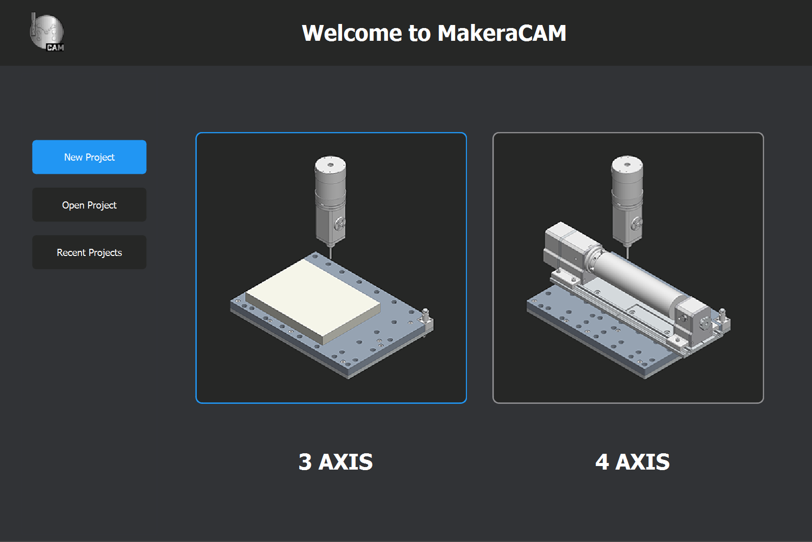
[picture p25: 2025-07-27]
assets/cam_section/makera_moment.PNG

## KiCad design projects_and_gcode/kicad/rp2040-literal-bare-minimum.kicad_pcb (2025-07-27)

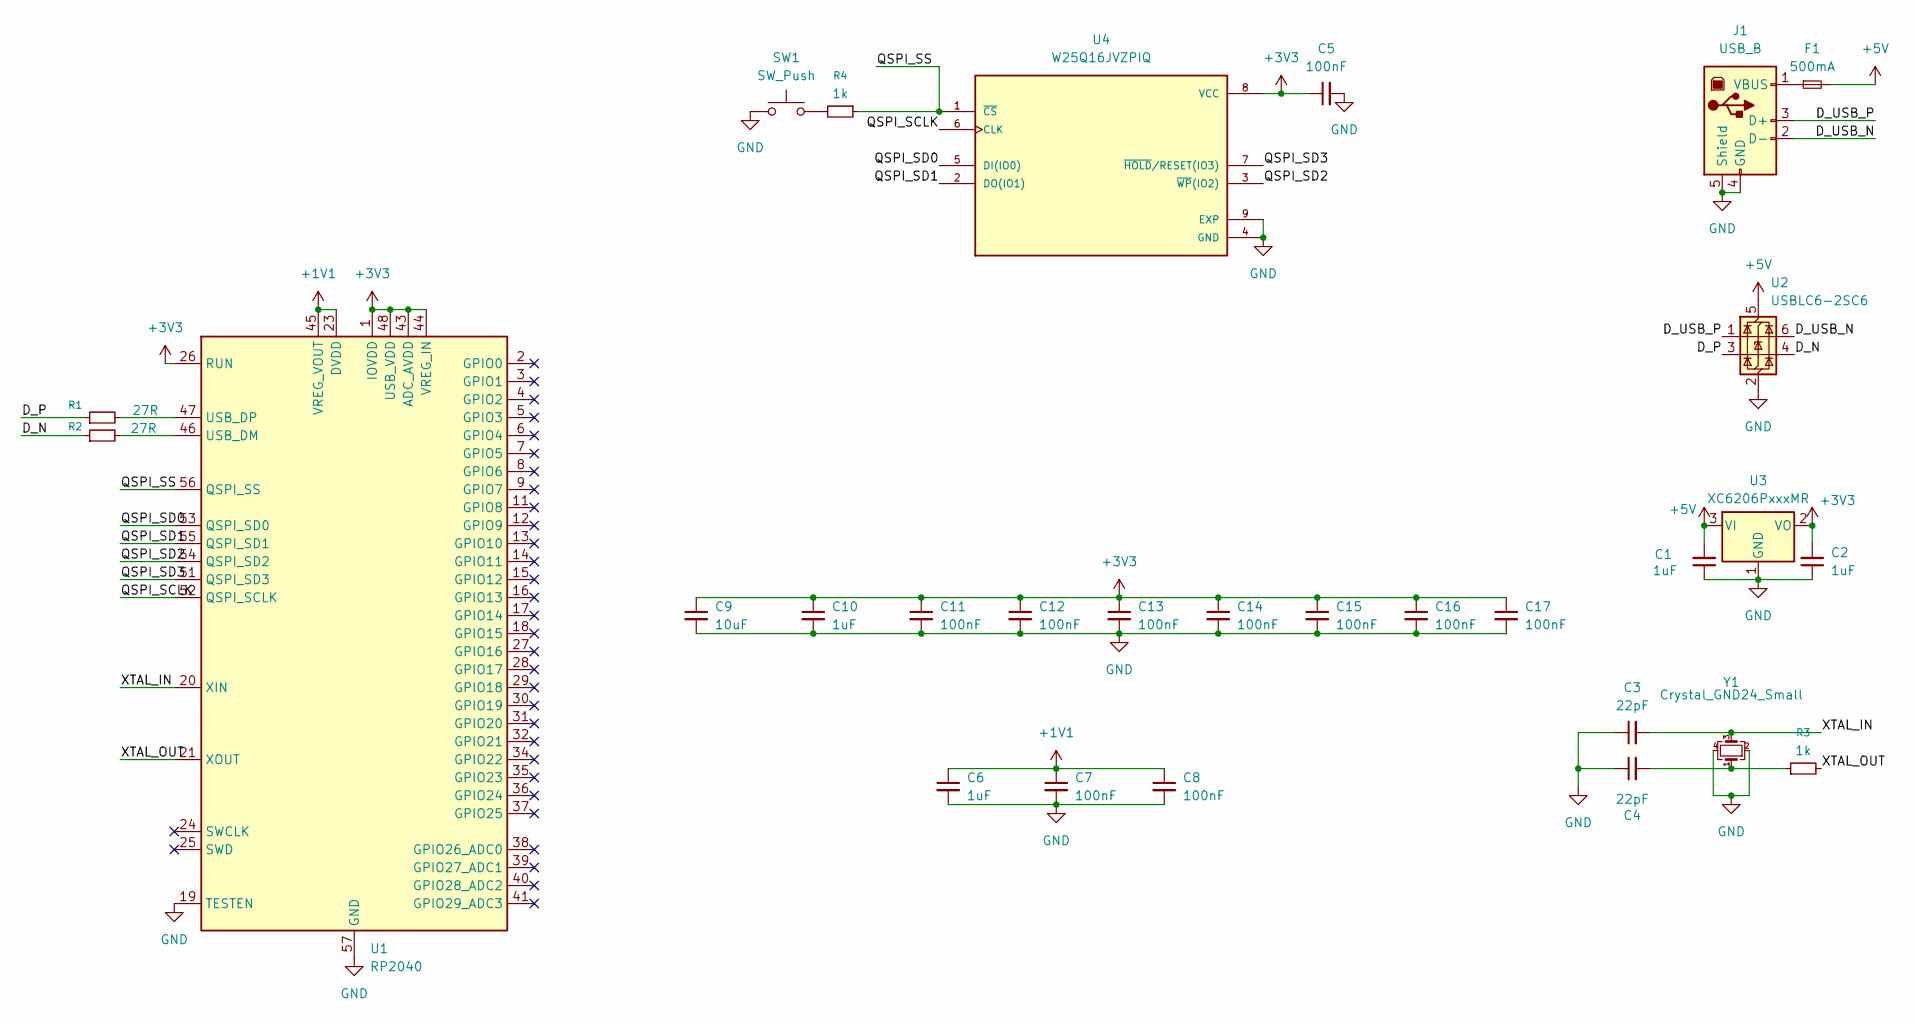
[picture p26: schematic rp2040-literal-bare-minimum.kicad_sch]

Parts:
C1, C2, C6, C10: 1uF; C_0402_1005Metric-notxt
C3, C4: 22pF; C_0402_1005Metric-notxt
C5, C7, C8, C11, C12, C13, C14, C15, C16, C17: 100nF; C_0402_1005Metric-notxt
C9: 10uF; C_0402_1005Metric-notxt
F1: 500mA; Fuse_1206_3216Metric-notxt
J1: USB_B; USB_B_Lumberg_2411_02_Horizontal-notxt
R1, R2: 27R; R_0402_1005Metric-notext
R3, R4: 1k; R_0402_1005Metric-notext
SW1: SW_Push; SW_SPST_EVQP2-notxt
U1: RP2040; QFN-56-1EP_7x7mm_P0.4mm_EP3.2x3.2mm
U2: USBLC6-2SC6; SOT-23-6
U3: XC6206PxxxMR; SOT-23-3
U4: W25Q16JVZPIQ; SON127P500X600X80-9N
Y1: Crystal_GND24_Small; Crystal_SMD_3225-4Pin_3.2x2.5mm-notxt

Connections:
+1V1: C6.1, C7.1, C8.1, U1.23 (DVDD), U1.45 (VREG_VOUT), U1.50 (DVDD)
+3V3: C2.2, C5.1, C9.1, C10.1, C11.1, C12.1, C13.1, C14.1, C15.1, C16.1, C17.1, U1.1 (IOVDD), U1.10 (IOVDD), U1.22 (IOVDD), U1.26 (RUN), U1.33 (IOVDD), U1.42 (IOVDD), U1.43 (ADC_AVDD), U1.44 (VREG_IN), U1.48 (USB_VDD), U1.49 (IOVDD), U3.2 (VO), U4.8 (VCC)
+5V: C1.2, F1.2, U2.5 (VBUS), U3.3 (VI)
/D_N: R2.1, U2.4 (I/O2)
/D_P: R1.1, U2.3 (I/O2)
/D_USB_N: J1.2 (D-), U2.6 (I/O1)
/D_USB_P: J1.3 (D+), U2.1 (I/O1)
/QSPI_SCLK: U1.52 (QSPI_SCLK), U4.6 (CLK)
/QSPI_SD0: U1.53 (QSPI_SD0), U4.5 (DI(IO0))
/QSPI_SD1: U1.55 (QSPI_SD1), U4.2 (DO(IO1))
/QSPI_SD2: U1.54 (QSPI_SD2), U4.3 (~WP(IO2))
/QSPI_SD3: U1.51 (QSPI_SD3), U4.7 (~HOLD/RESET(IO3))
/QSPI_SS: R4.1, U1.56 (QSPI_SS), U4.1 (~CS)
/XTAL_IN: C3.2, U1.20 (XIN), Y1.3
/XTAL_OUT: R3.2, U1.21 (XOUT)
GND: C1.1, C2.1, C3.1, C4.1, C5.2, C6.2, C7.2, C8.2, C9.2, C10.2, C11.2, C12.2, C13.2, C14.2, C15.2, C16.2, C17.2, J1.4 (GND), J1.5 (Shield), SW1.1, U1.19 (TESTEN), U1.57 (GND), U2.2 (GND), U3.1 (GND), U4.4 (GND), U4.9 (EXP), Y1.2, Y1.4
unnamed: C4.2, R3.1, Y1.1
unnamed: F1.1, J1.1 (VBUS)
unnamed: R4.2, SW1.2
unnamed: R2.2, U1.46 (USB_DM)
unnamed: R1.2, U1.47 (USB_DP)

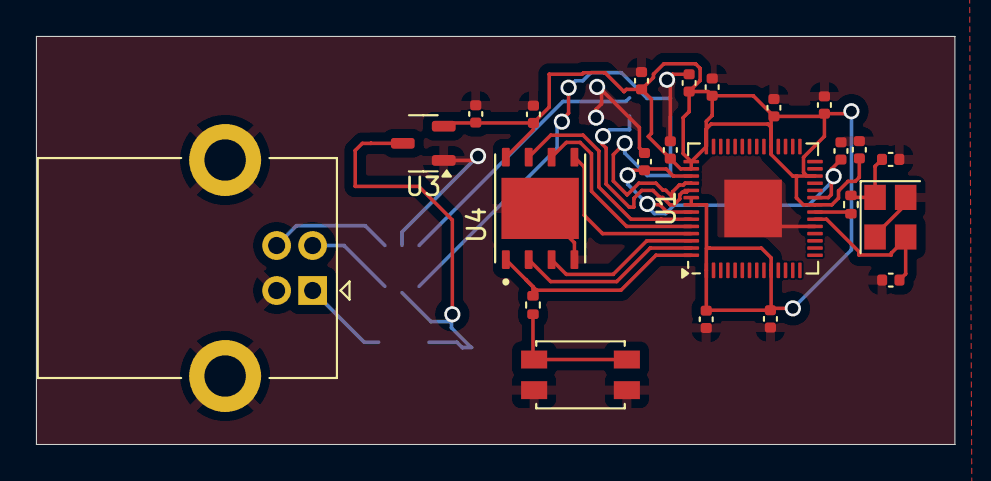
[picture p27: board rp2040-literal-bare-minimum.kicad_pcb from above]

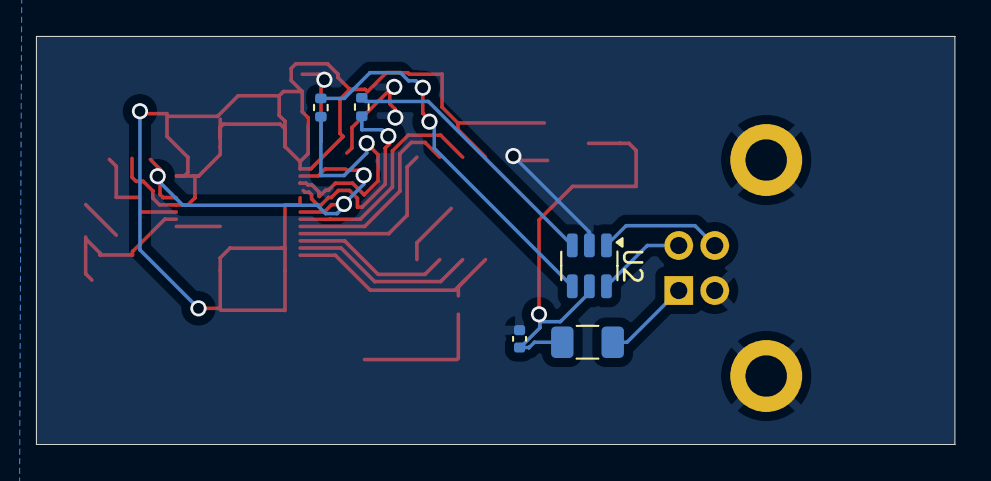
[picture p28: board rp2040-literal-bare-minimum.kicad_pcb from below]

Board: 2 copper layers, 51.0 x 22.7 mm, 28 parts (5 on the bottom side), 21 nets.

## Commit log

2025-07-27 lotta cad shit
    [rp2040-literal-bare-minimum-B_Cu.gbr, rp2040-literal-bare-minimum-B_Mask.gbr, rp2040-literal-bare-minimum-B_Silkscreen.gbr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]
2025-07-27 the software side is done, gotta do the actual milling side now
    [PCB fixture thing.f3d, PCB fixture thing.step, Spindle Fan.step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]
2025-07-28 mirror vertically
    [flatcam_flipped_rp2040-literal-bare-minimum-B_Cu.gbr.GBR]
